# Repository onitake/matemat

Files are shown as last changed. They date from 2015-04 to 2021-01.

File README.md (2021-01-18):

# Matemat

The Matemat is a vending machine for carbonated soft drinks.

It is based on an old vending machine with all its electronics replaced by new
custom-build circuit boards.

All hardware and software was designed by members of
[CCC Basel](http://www.ccc-basel.ch) and released in the form of circuit
diagrams, printed circuit board layouts and source code for anyone to use and
modify. Refer to the LICENSE file for details.

The name "Matemat" is a portmanteau of "mate" (as in mate tea) and "automat"
(the German word for vending machine). The device is mainly intended to dispense
mate tea based soft drinks, but may be used for other types of beverages too.

## Structure

The heart of the vending machine is a Raspberry Pi model 3 or zero or later,
with a custom CAN interface board on its GPIO header.

See [CAN Hat](https://github.com/onitake/canhat) for more information.

## Firmware

Some of the modules require firmware. There is a makefile in each module's
firmware directory to build and flash the firmware to the integrated
microcontroller

Before building, you need to check out the CAN driver source code, which is
referenced as a Git submodule.

Run the following commands in the checked out repository:

```shell
git submodule init
git submodule update
```

## Modules

The Matemat components are highly modular. Individual circuits are connected by
CAN bus, and can be extended as needed.

### drive

Single-motor driver.

Attached directly to each bottle release mechanism. Requires only power supply
wires for the motor and the CAN bus line.

### power

Motor driver board and power supply.

Alternative to the drive board. Uses the existing machine wiring instead of
power + CAN.

### control

Old central control board. Obsolete.

### feedback

End switch feedback interface.

Senses the status of the end switches and sends CAN bus messages on changes.

This module requires firmware. Connect an Atmel programmer to the ISP header,
change into the firmware directory `feedback/firmware/` and run:

```shell
make flash
```

### poweriface

Interface between CAN bus and power board.

This module requires firmware. Connect an Atmel programmer to the ISP header,
change into the firmware directory `poweriface/firmware/` and run:

```shell
make flash
```

### sensor

Environment sensor interface.

### wiring

Wring schema of the old vending machine.

## Bus

### Topology

All modules are connected via a CAN bus. It is highly recommended to wire them
by means of shielded twisted-pair cable with a nominal impedance of 120Ω.
At the very least, you need a cable with three wires to ensure a good ground
connection between all modules.

To allow for easy wiring, six-pole screw terminals are mounted to the PCBs.
Two poles are intended for the positive CAN bus line, two for the negative line
and two for the shield. They are internally connected together.

### Wiring

To achieve a continuous bus topology, connect only two cables to each module.
Make sure CAN H is connected to CAN H and CAN L to CAN L. Crossover is not
supported on the CAN bus. When wiring is complete, you should end up with a
continuous bus that is tapped at each module. Attach 120Ω resistors (preferably
1% or better) to the ends of the bus.

The final wiring should look like this:

```
┌───────────┐   ┌───────────┐   ┌───────────┐
│  module1  │   │  module2  │   │  module3  │
│           │   │           │   │           │
│H L ⏚ H L ⏚│   │H L ⏚ H L ⏚│   │H L ⏚ H L ⏚│
└╥─╥─╥─╥─╥─╥┘   └╥─╥─╥─╥─╥─╥┘   └╥─╥─╥─╥─╥─╥┘
 ╰━╯   └╥┘╱      └╥┘╱  └╥┘╱      └╥┘╱  ╰━╯
 120Ω   ║╱        ║╱    ║╱        ║╱   120Ω
        ╚═════════╝     ╚═════════╝
```

### Protocol

Bus communication only makes use of basic CAN features. No higher-level
protocols such as CiA, EtherCAN, VSCP or similar are required.

Normal 11-bit CAN adressing mode is used. For messages that support RTR, any
module can send a remote transmission request and the addressed module will
respond with the described message. A module may also send the message
without being probed.

This is the list of supported message IDs:

| Message ID | Sender | Receiver | RTR Support? |Data Length | Data Format | Description |
|---|---|---|---|---|---|---|
| 0x10 | feedback | any | yes | 2 | 0b00000KJI 0bHGFEDCBA | Feedback module status report (A..E = end switch D..H, F..J = empty switch D..H, K = reset switch, 0 = off, 1 = on) |
| 0x11 | poweriface | any | yes | 2 | 0bHHHHHHHH 0bLLLLLLLL | Power module status report (0xHHLL are the contents of the 16-bit shift register) |
| 0x21 | controller | poweriface | no | 1 | 0b00000MMM | Start dispensing from slot M (1-5) or stop all dispensers (M = 0) |
| 0x4f | any | any | no | 1 | 0b0000000E | Enable (E = 1) or disable (E = 0) automatic status updates on all modules |

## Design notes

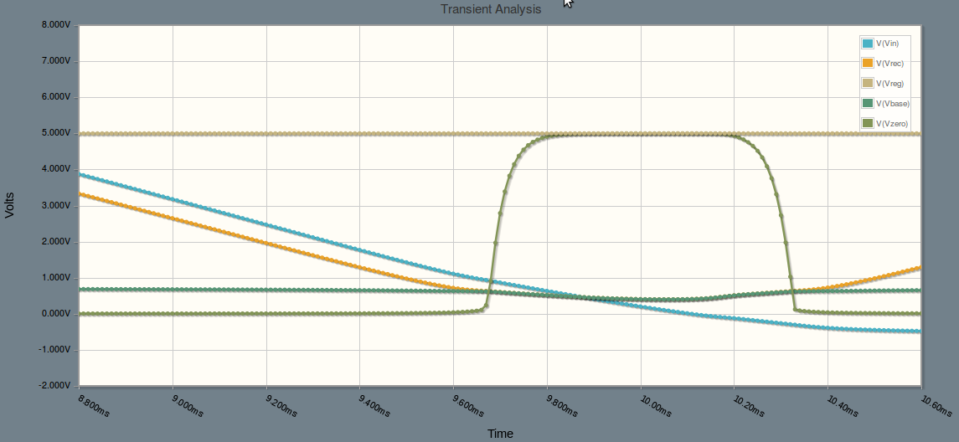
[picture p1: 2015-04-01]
zerocross.png

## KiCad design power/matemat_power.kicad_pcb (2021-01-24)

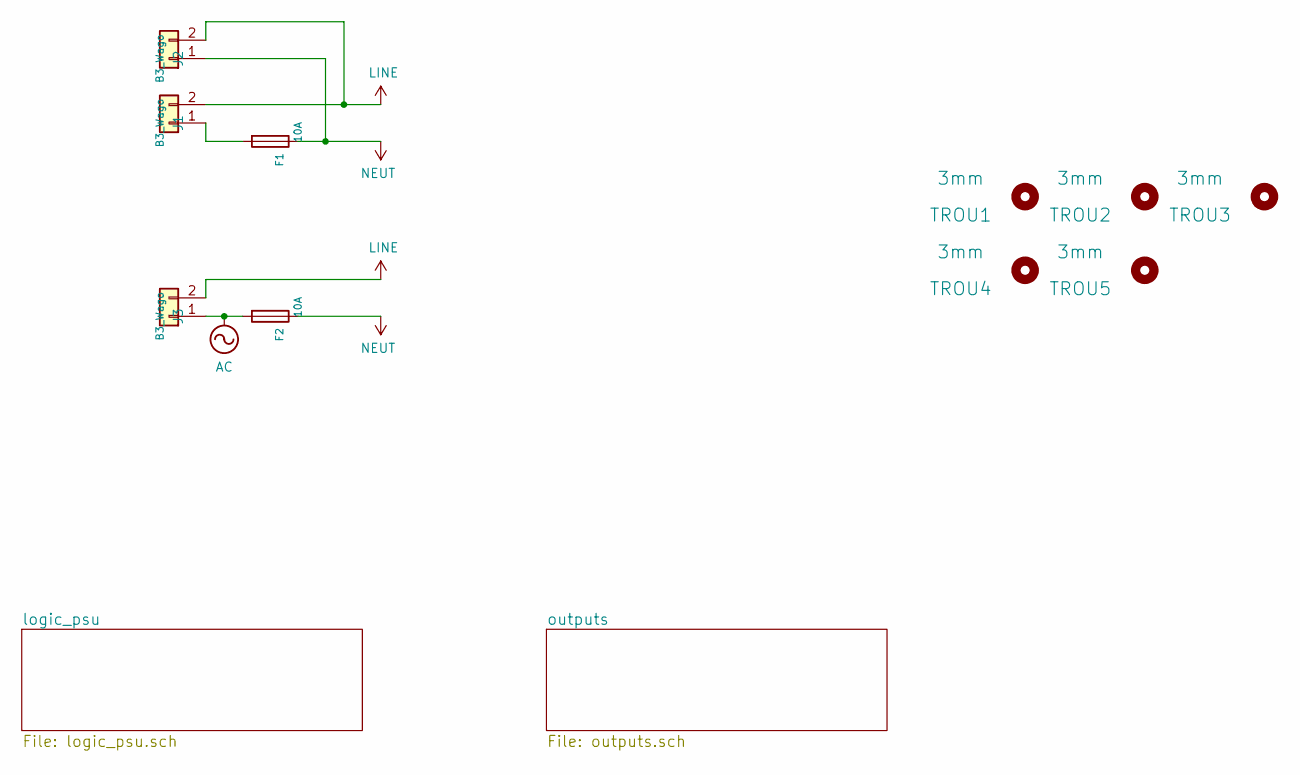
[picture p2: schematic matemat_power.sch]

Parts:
F1, F2: 10A; Fuseholder_Cylinder-5x20mm_Schurter_0031_8201_Horizontal_Op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
J1, J2, J3: B3_Wago; TerminalBlock_WAGO_236-402_1x02_P5.00mm_45Degree
TROU1, TROU2, TROU3, TROU4, TROU5: 3mm; MountingHole_3.2mm_M3

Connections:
AC: F2.2, J3.1; also elsewhere on the board
LINE: J1.2, J2.2, J3.2; also elsewhere on the board
NEUT: F1.1, F2.1, J2.1; also elsewhere on the board
unnamed: F1.2, J1.1

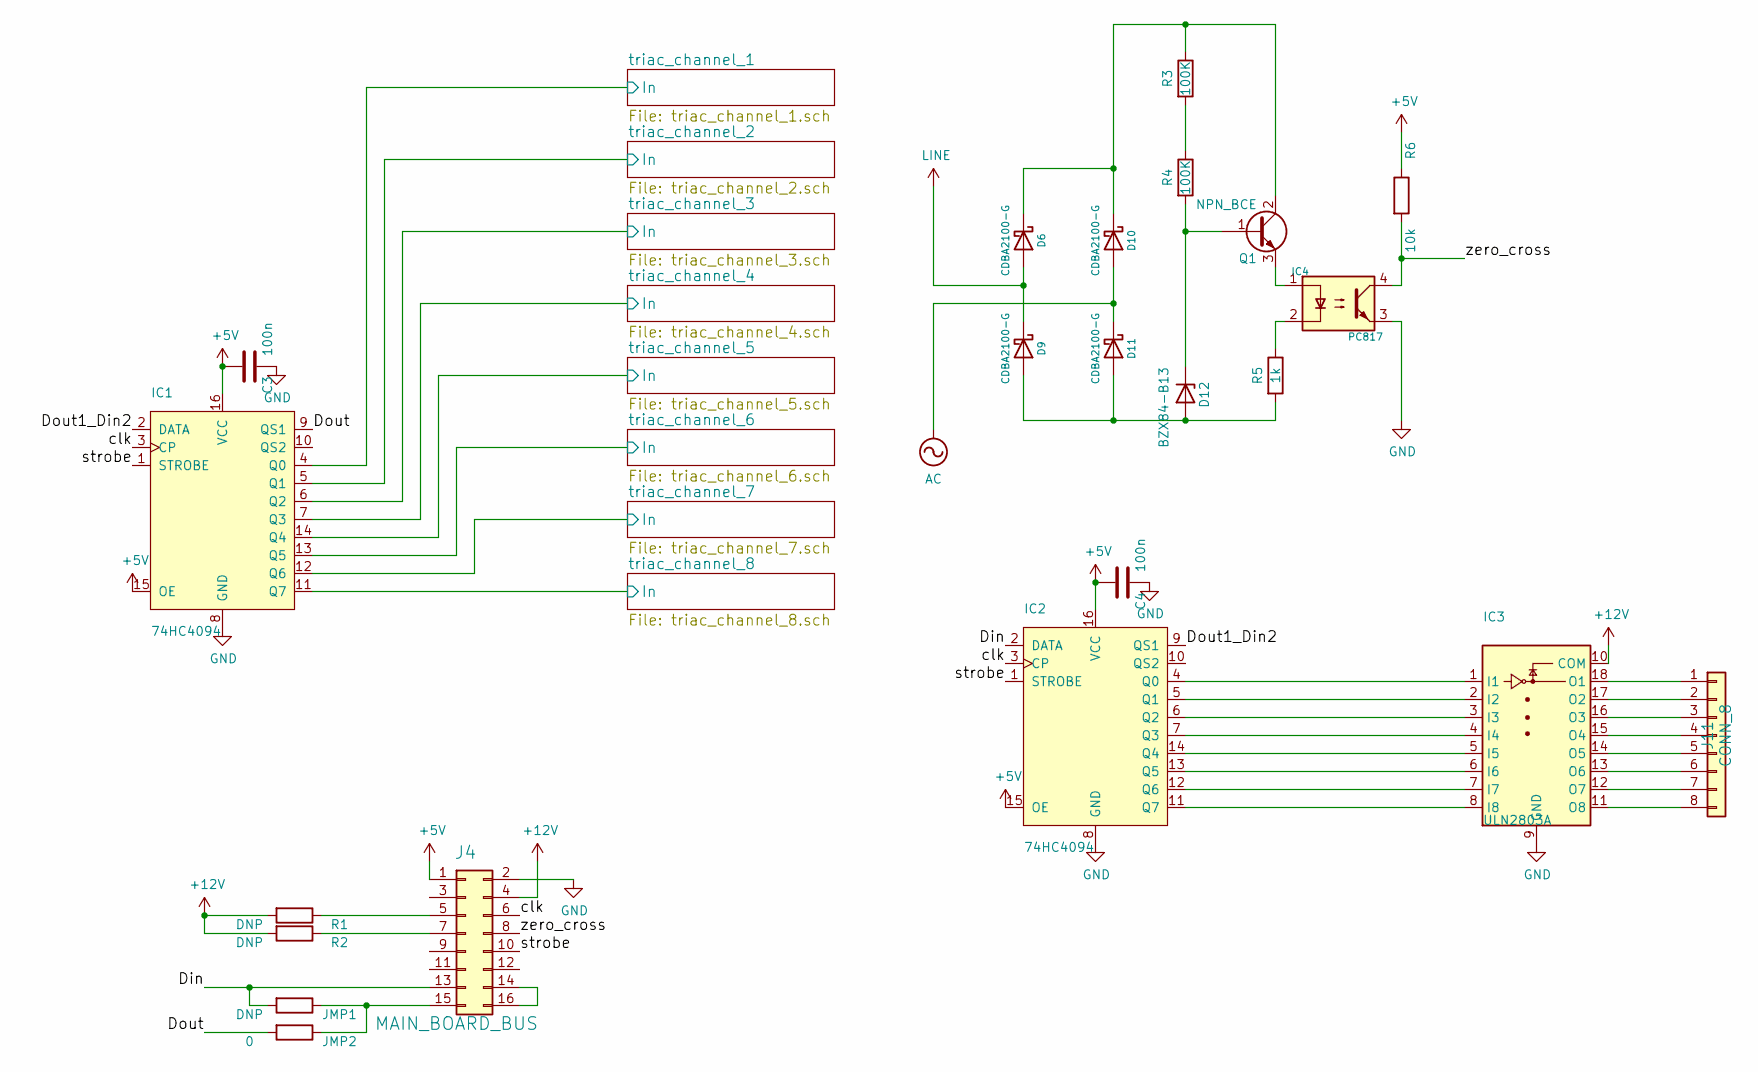
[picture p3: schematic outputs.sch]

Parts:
C3, C4: 100n; C_0805_2012Metric_Pad1.18x1.45mm_HandSolder
D6, D9, D10, D11: CDBA2100-G; D_SMA
D12: BZX84-B13; D_SOT-23_ANK
IC1, IC2: 74HC4094; SOIC-16_3.9x9.9mm_P1.27mm
IC3: ULN2803A; SOIC-18W_7.5x11.6mm_P1.27mm
IC4: PC817; DIP-4_W7.62mm
J4: MAIN_BOARD_BUS; PinHeader_2x08_P2.54mm_Vertical
J11: CONN_8; TerminalBlock_Phoenix_MPT-0,5-8-2.54_1x08_P2.54mm_Horizontal
JMP1: DNP; R_0603_1608Metric_Pad0.98x0.95mm_HandSolder
JMP2: 0; R_0603_1608Metric_Pad0.98x0.95mm_HandSolder
Q1: NPN_BCE; TO-220-3_Vertical
R1, R2: DNP; R_0603_1608Metric_Pad0.98x0.95mm_HandSolder
R3, R4: 100K; R_Axial_DIN0309_L9.0mm_D3.2mm_P12.70mm_Horizontal
R5: 1k; R_0805_2012Metric_Pad1.20x1.40mm_HandSolder
R6: 10k; R_0805_2012Metric_Pad1.20x1.40mm_HandSolder

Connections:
+5V: C3.2, C4.2, IC1.15 (OE), IC1.16 (VCC), IC2.15 (OE), IC2.16 (VCC), J4.1, R6.1
+12V: IC3.10 (COM), J4.4, R1.2, R2.2; also elsewhere on the board
/outputs/Din: IC2.2 (DATA), J4.13, JMP1.2
/outputs/Dout: IC1.9 (QS1), JMP2.2
/outputs/Dout1_Din2: IC1.2 (DATA), IC2.9 (QS1)
/outputs/clk: IC1.3 (CP), IC2.3 (CP), J4.6
/outputs/strobe: IC1.1 (STROBE), IC2.1 (STROBE), J4.10
/outputs/triac_channel_1/In: IC1.4 (Q0); also elsewhere on the board
/outputs/triac_channel_2/In: IC1.5 (Q1); also elsewhere on the board
/outputs/triac_channel_3/In: IC1.6 (Q2); also elsewhere on the board
/outputs/triac_channel_4/In: IC1.7 (Q3); also elsewhere on the board
/outputs/triac_channel_5/In: IC1.14 (Q4); also elsewhere on the board
/outputs/triac_channel_6/In: IC1.13 (Q5); also elsewhere on the board
/outputs/triac_channel_7/In: IC1.12 (Q6); also elsewhere on the board
/outputs/triac_channel_8/In: IC1.11 (Q7); also elsewhere on the board
/outputs/zero_cross: IC4.4, J4.8, R6.2
AC: D10.2 (A), D11.1 (K); also elsewhere on the board
GND: C3.1, C4.1, IC1.8 (GND), IC2.8 (GND), IC3.9 (GND), IC4.3, J4.2; also elsewhere on the board
LINE: D6.2 (A), D9.1 (K); also elsewhere on the board
unnamed: D6.1 (K), D10.1 (K), Q1.2 (C), R3.1
unnamed: D9.2 (A), D11.2 (A), D12.2 (A), R5.2
unnamed: D12.1 (K), Q1.1 (B), R4.2
unnamed: IC2.4 (Q0), IC3.1 (I1)
unnamed: IC2.5 (Q1), IC3.2 (I2)
unnamed: IC2.6 (Q2), IC3.3 (I3)
unnamed: IC2.7 (Q3), IC3.4 (I4)
unnamed: IC2.11 (Q7), IC3.8 (I8)
unnamed: IC2.12 (Q6), IC3.7 (I7)
unnamed: IC2.13 (Q5), IC3.6 (I6)
unnamed: IC2.14 (Q4), IC3.5 (I5)
unnamed: IC3.11 (O8), J11.8
unnamed: IC3.12 (O7), J11.7
unnamed: IC3.13 (O6), J11.6
unnamed: IC3.14 (O5), J11.5
unnamed: IC3.15 (O4), J11.4
unnamed: IC3.16 (O3), J11.3
unnamed: IC3.17 (O2), J11.2
unnamed: IC3.18 (O1), J11.1
unnamed: IC4.1, Q1.3 (E)
unnamed: IC4.2, R5.1
unnamed: J4.5, R1.1
unnamed: J4.7, R2.1
unnamed: J4.14, J4.16
unnamed: J4.15, JMP1.1, JMP2.1
unnamed: R3.2, R4.1

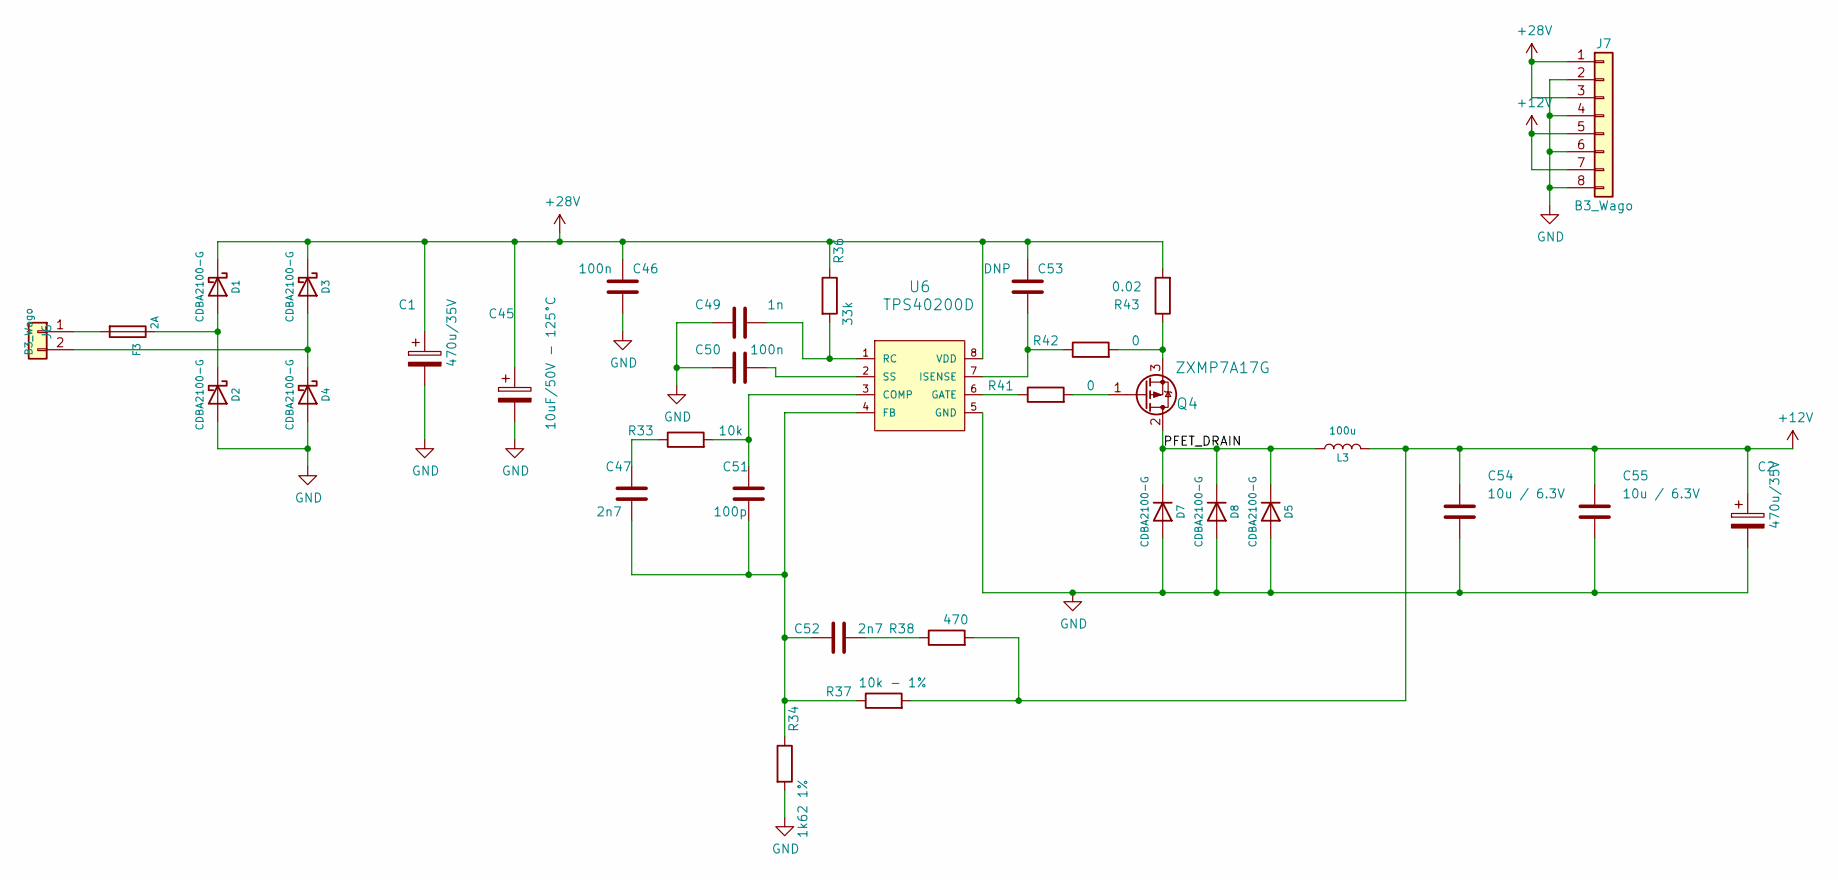
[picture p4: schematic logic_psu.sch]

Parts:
C1, C2: 470u/35V; CP_Radial_D10.0mm_P5.00mm
C45: 10uF/50V - 125°C; CP_Radial_D10.0mm_P5.00mm
C46, C50: 100n; C_0805_2012Metric_Pad1.18x1.45mm_HandSolder
C47, C52: 2n7; C_0805_2012Metric_Pad1.18x1.45mm_HandSolder
C49: 1n; C_0805_2012Metric_Pad1.18x1.45mm_HandSolder
C51: 100p; C_0805_2012Metric_Pad1.18x1.45mm_HandSolder
C53: DNP; C_0805_2012Metric_Pad1.18x1.45mm_HandSolder
C54, C55: 10u / 6.3V; C_0805_2012Metric_Pad1.18x1.45mm_HandSolder
D1, D2, D3, D4, D5, D7, D8: CDBA2100-G; D_SMA
F3: 2A; Fuseholder_Cylinder-5x20mm_Schurter_0031_8201_Horizontal_Op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
J6: B3_Wago; TerminalBlock_WAGO_236-402_1x02_P5.00mm_45Degree
J7: B3_Wago; TerminalBlock_WAGO_236-408_1x08_P5.00mm_45Degree
L3: 100u; L_Toroid_Vertical_L22.4mm_W10.2mm_P7.90mm_Vishay_TJ4
Q4: ZXMP7A17G; SOT-223-3_TabPin2
R33: 10k; R_0805_2012Metric_Pad1.20x1.40mm_HandSolder
R34: 1k62 1%; R_0805_2012Metric_Pad1.20x1.40mm_HandSolder
R36: 33k; R_0805_2012Metric_Pad1.20x1.40mm_HandSolder
R37: 10k - 1%; R_0805_2012Metric_Pad1.20x1.40mm_HandSolder
R38: 470; R_0805_2012Metric_Pad1.20x1.40mm_HandSolder
R41, R42: 0; R_0805_2012Metric_Pad1.20x1.40mm_HandSolder
R43: 0.02; R_2010_5025Metric_Pad1.40x2.65mm_HandSolder
U6: TPS40200D; SOIC-8_3.9x4.9mm_P1.27mm

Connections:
+12V: C2.1, C54.1, C55.1, J7.5, J7.7, L3.2, R37.2, R38.2; also elsewhere on the board
+28V: C1.1, C45.1, C46.1, C53.1, D1.1 (K), D3.1 (K), J7.1, J7.3, R36.1, R43.2, U6.8 (VDD)
/logic_psu/PFET_DRAIN: D5.1 (K), D7.1 (K), D8.1 (K), L3.1, Q4.2 (D)
GND: C1.2, C2.2, C45.2, C46.2, C49.1, C50.1, C54.2, C55.2, D2.2 (A), D4.2 (A), D5.2 (A), D7.2 (A), D8.2 (A), J7.2, J7.4, J7.6, J7.8, R34.2, U6.5 (GND); also elsewhere on the board
unnamed: C47.1, R33.1
unnamed: C47.2, C51.2, C52.1, R34.1, R37.1, U6.4 (FB)
unnamed: C49.2, R36.2, U6.1 (RC)
unnamed: C50.2, U6.2 (SS)
unnamed: C51.1, R33.2, U6.3 (COMP)
unnamed: C52.2, R38.1
unnamed: C53.2, R42.1, U6.7 (ISENSE)
unnamed: D1.2 (A), D2.1 (K), F3.1
unnamed: D3.2 (A), D4.1 (K), J6.2
unnamed: F3.2, J6.1
unnamed: Q4.1 (G), R41.2
unnamed: Q4.3 (S), R42.2, R43.1
unnamed: R41.1, U6.6 (GATE)

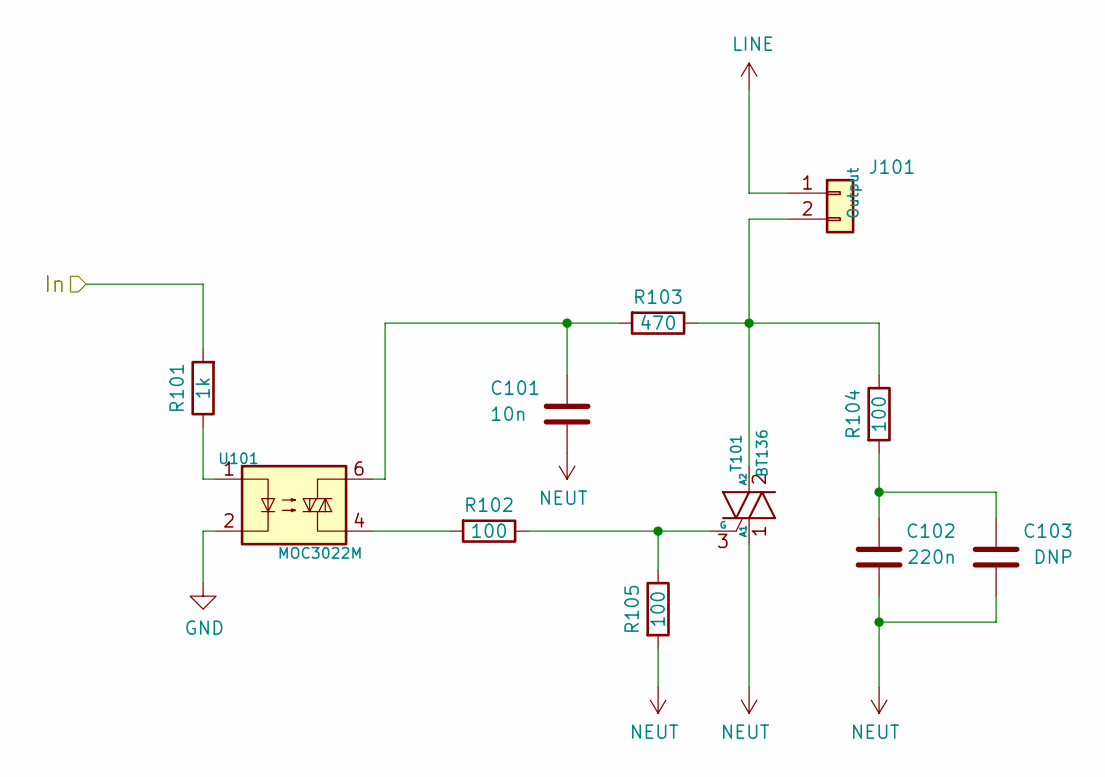
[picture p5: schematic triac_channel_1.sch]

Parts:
C101: 10n; C_Rect_L7.0mm_W2.5mm_P5.00mm
C102: 220n; C_Rect_L18.0mm_W5.0mm_P15.00mm_FKS3_FKP3
C103: DNP; C_Rect_L13.0mm_W4.0mm_P10.00mm_FKS3_FKP3_MKS4
J101: Output; TerminalBlock_WAGO_236-402_1x02_P5.00mm_45Degree
R101: 1k; R_0805_2012Metric_Pad1.20x1.40mm_HandSolder
R102, R104: 100; R_Axial_DIN0309_L9.0mm_D3.2mm_P12.70mm_Horizontal
R103: 470; R_Axial_DIN0309_L9.0mm_D3.2mm_P12.70mm_Horizontal
R105: 100; R_0805_2012Metric_Pad1.20x1.40mm_HandSolder
T101: BT136; TO-220-3_Vertical
U101: MOC3022M; DIP-6_W7.62mm_LongPads

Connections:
/outputs/triac_channel_1/In: R101.2; also elsewhere on the board
GND: U101.2; also elsewhere on the board
LINE: J101.1; also elsewhere on the board
NEUT: C101.2, C102.2, C103.2, R105.2, T101.1 (A1); also elsewhere on the board
unnamed: C101.1, R103.2, U101.6
unnamed: C102.1, C103.1, R104.2
unnamed: J101.2, R103.1, R104.1, T101.2 (A2)
unnamed: R101.1, U101.1
unnamed: R102.1, R105.1, T101.3 (G)
unnamed: R102.2, U101.4

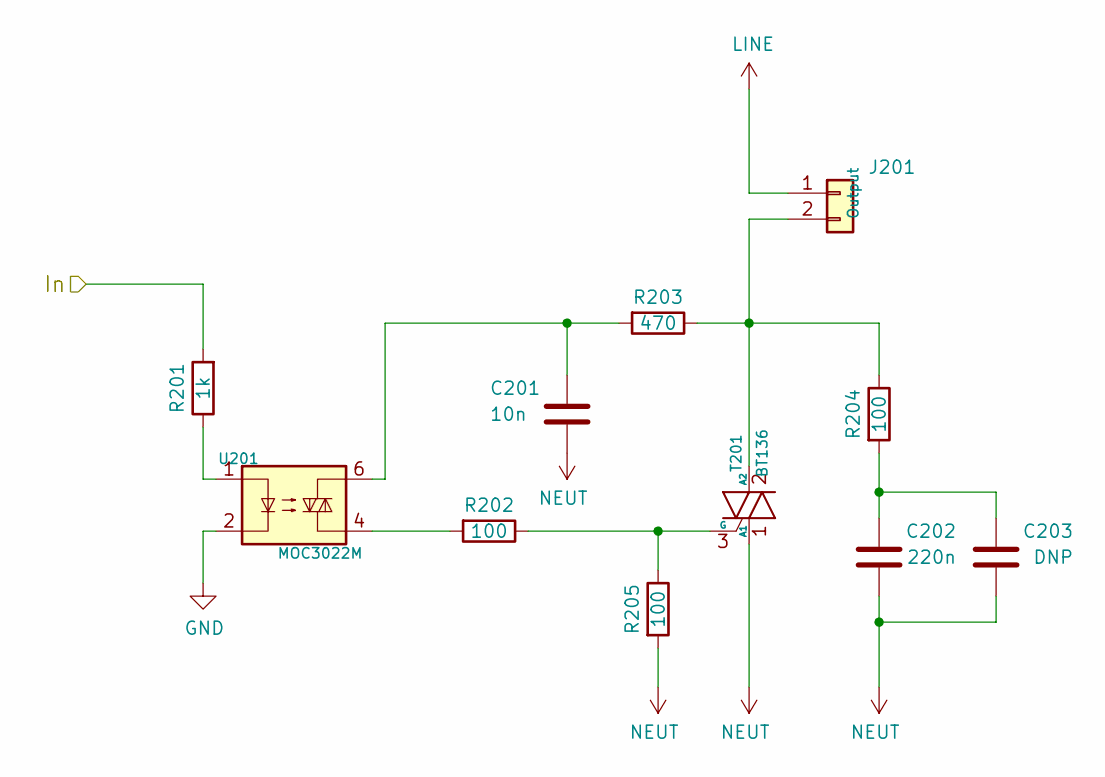
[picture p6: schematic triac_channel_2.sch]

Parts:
C201: 10n; C_Rect_L7.0mm_W2.5mm_P5.00mm
C202: 220n; C_Rect_L18.0mm_W5.0mm_P15.00mm_FKS3_FKP3
C203: DNP; C_Rect_L13.0mm_W4.0mm_P10.00mm_FKS3_FKP3_MKS4
J201: Output; TerminalBlock_WAGO_236-402_1x02_P5.00mm_45Degree
R201: 1k; R_0805_2012Metric_Pad1.20x1.40mm_HandSolder
R202, R204: 100; R_Axial_DIN0309_L9.0mm_D3.2mm_P12.70mm_Horizontal
R203: 470; R_Axial_DIN0309_L9.0mm_D3.2mm_P12.70mm_Horizontal
R205: 100; R_0805_2012Metric_Pad1.20x1.40mm_HandSolder
T201: BT136; TO-220-3_Vertical
U201: MOC3022M; DIP-6_W7.62mm_LongPads

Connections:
/outputs/triac_channel_2/In: R201.2; also elsewhere on the board
GND: U201.2; also elsewhere on the board
LINE: J201.1; also elsewhere on the board
NEUT: C201.2, C202.2, C203.2, R205.2, T201.1 (A1); also elsewhere on the board
unnamed: C201.1, R203.2, U201.6
unnamed: C202.1, C203.1, R204.2
unnamed: J201.2, R203.1, R204.1, T201.2 (A2)
unnamed: R201.1, U201.1
unnamed: R202.1, R205.1, T201.3 (G)
unnamed: R202.2, U201.4

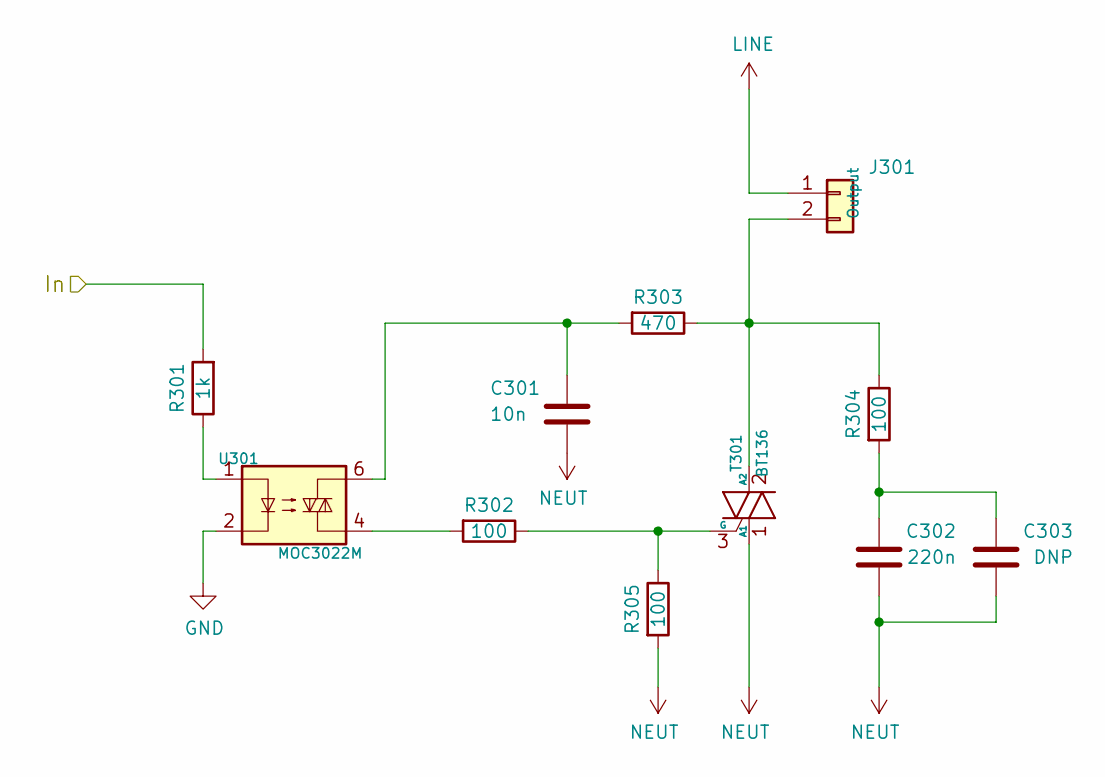
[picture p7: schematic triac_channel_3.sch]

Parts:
C301: 10n; C_Rect_L7.0mm_W2.5mm_P5.00mm
C302: 220n; C_Rect_L18.0mm_W5.0mm_P15.00mm_FKS3_FKP3
C303: DNP; C_Rect_L13.0mm_W4.0mm_P10.00mm_FKS3_FKP3_MKS4
J301: Output; TerminalBlock_WAGO_236-402_1x02_P5.00mm_45Degree
R301: 1k; R_0805_2012Metric_Pad1.20x1.40mm_HandSolder
R302, R304: 100; R_Axial_DIN0309_L9.0mm_D3.2mm_P12.70mm_Horizontal
R303: 470; R_Axial_DIN0309_L9.0mm_D3.2mm_P12.70mm_Horizontal
R305: 100; R_0805_2012Metric_Pad1.20x1.40mm_HandSolder
T301: BT136; TO-220-3_Vertical
U301: MOC3022M; DIP-6_W7.62mm_LongPads

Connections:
/outputs/triac_channel_3/In: R301.2; also elsewhere on the board
GND: U301.2; also elsewhere on the board
LINE: J301.1; also elsewhere on the board
NEUT: C301.2, C302.2, C303.2, R305.2, T301.1 (A1); also elsewhere on the board
unnamed: C301.1, R303.2, U301.6
unnamed: C302.1, C303.1, R304.2
unnamed: J301.2, R303.1, R304.1, T301.2 (A2)
unnamed: R301.1, U301.1
unnamed: R302.1, R305.1, T301.3 (G)
unnamed: R302.2, U301.4

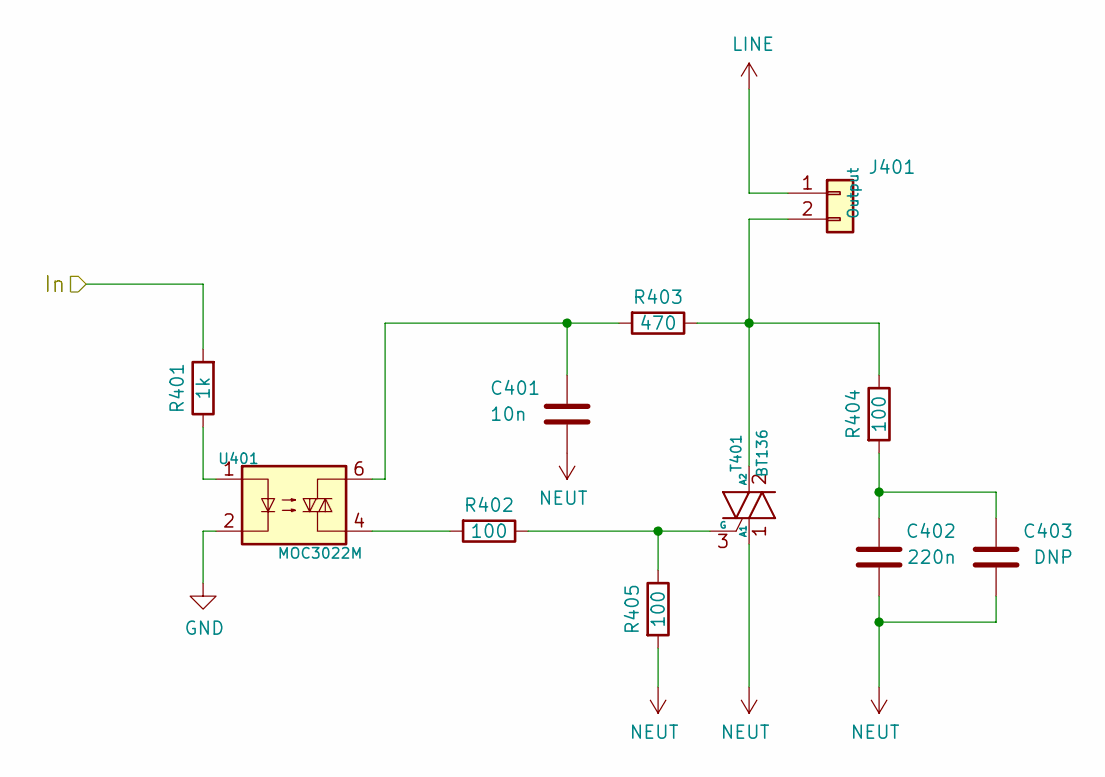
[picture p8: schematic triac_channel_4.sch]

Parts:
C401: 10n; C_Rect_L7.0mm_W2.5mm_P5.00mm
C402: 220n; C_Rect_L18.0mm_W5.0mm_P15.00mm_FKS3_FKP3
C403: DNP; C_Rect_L13.0mm_W4.0mm_P10.00mm_FKS3_FKP3_MKS4
J401: Output; TerminalBlock_WAGO_236-402_1x02_P5.00mm_45Degree
R401: 1k; R_0805_2012Metric_Pad1.20x1.40mm_HandSolder
R402, R404: 100; R_Axial_DIN0309_L9.0mm_D3.2mm_P12.70mm_Horizontal
R403: 470; R_Axial_DIN0309_L9.0mm_D3.2mm_P12.70mm_Horizontal
R405: 100; R_0805_2012Metric_Pad1.20x1.40mm_HandSolder
T401: BT136; TO-220-3_Vertical
U401: MOC3022M; DIP-6_W7.62mm_LongPads

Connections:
/outputs/triac_channel_4/In: R401.2; also elsewhere on the board
GND: U401.2; also elsewhere on the board
LINE: J401.1; also elsewhere on the board
NEUT: C401.2, C402.2, C403.2, R405.2, T401.1 (A1); also elsewhere on the board
unnamed: C401.1, R403.2, U401.6
unnamed: C402.1, C403.1, R404.2
unnamed: J401.2, R403.1, R404.1, T401.2 (A2)
unnamed: R401.1, U401.1
unnamed: R402.1, R405.1, T401.3 (G)
unnamed: R402.2, U401.4

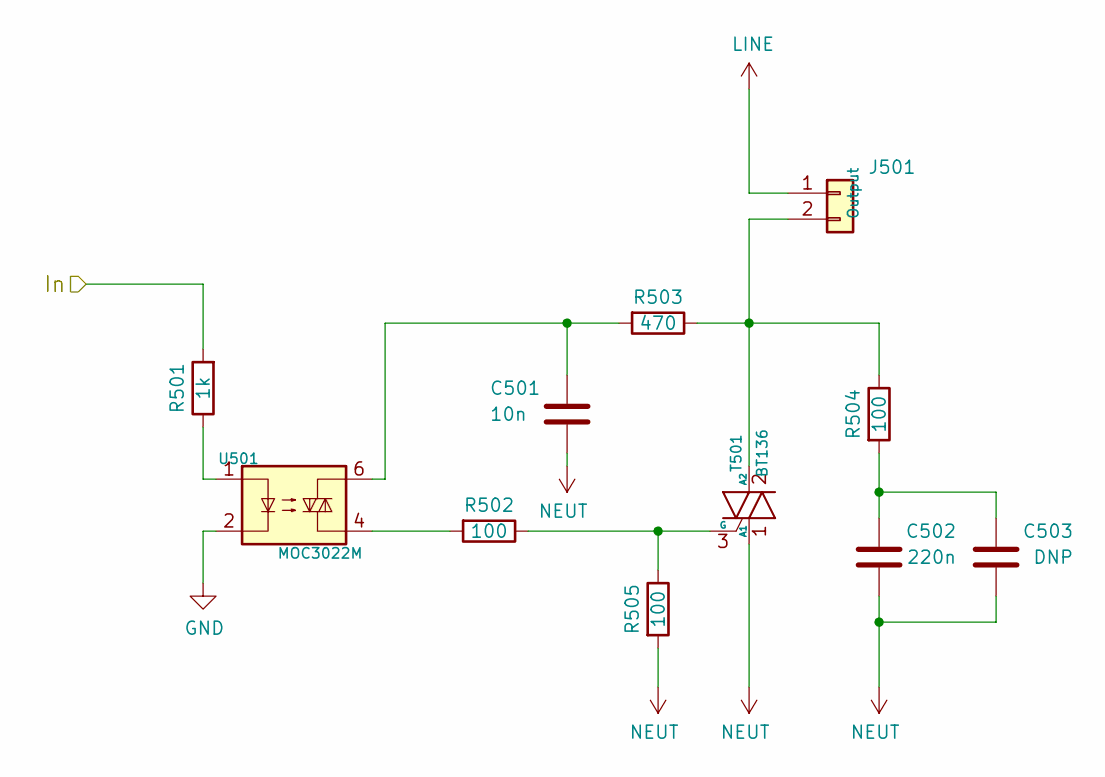
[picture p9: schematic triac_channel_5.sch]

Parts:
C501: 10n; C_Rect_L7.0mm_W2.5mm_P5.00mm
C502: 220n; C_Rect_L18.0mm_W5.0mm_P15.00mm_FKS3_FKP3
C503: DNP; C_Rect_L13.0mm_W4.0mm_P10.00mm_FKS3_FKP3_MKS4
J501: Output; TerminalBlock_WAGO_236-402_1x02_P5.00mm_45Degree
R501: 1k; R_0805_2012Metric_Pad1.20x1.40mm_HandSolder
R502, R504: 100; R_Axial_DIN0309_L9.0mm_D3.2mm_P12.70mm_Horizontal
R503: 470; R_Axial_DIN0309_L9.0mm_D3.2mm_P12.70mm_Horizontal
R505: 100; R_0805_2012Metric_Pad1.20x1.40mm_HandSolder
T501: BT136; TO-220-3_Vertical
U501: MOC3022M; DIP-6_W7.62mm_LongPads

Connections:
/outputs/triac_channel_5/In: R501.2; also elsewhere on the board
GND: U501.2; also elsewhere on the board
LINE: J501.1; also elsewhere on the board
NEUT: C501.2, C502.2, C503.2, R505.2, T501.1 (A1); also elsewhere on the board
unnamed: C501.1, R503.2, U501.6
unnamed: C502.1, C503.1, R504.2
unnamed: J501.2, R503.1, R504.1, T501.2 (A2)
unnamed: R501.1, U501.1
unnamed: R502.1, R505.1, T501.3 (G)
unnamed: R502.2, U501.4

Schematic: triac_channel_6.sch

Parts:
C601: 10n; C_Rect_L7.0mm_W2.5mm_P5.00mm
C602: 220n; C_Rect_L18.0mm_W5.0mm_P15.00mm_FKS3_FKP3
C603: DNP; C_Rect_L13.0mm_W4.0mm_P10.00mm_FKS3_FKP3_MKS4
J601: Output; TerminalBlock_WAGO_236-402_1x02_P5.00mm_45Degree
R601: 1k; R_0805_2012Metric_Pad1.20x1.40mm_HandSolder
R602, R604: 100; R_Axial_DIN0309_L9.0mm_D3.2mm_P12.70mm_Horizontal
R603: 470; R_Axial_DIN0309_L9.0mm_D3.2mm_P12.70mm_Horizontal
R605: 100; R_0805_2012Metric_Pad1.20x1.40mm_HandSolder
T601: BT136; TO-220-3_Vertical
U601: MOC3022M; DIP-6_W7.62mm_LongPads

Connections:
/outputs/triac_channel_6/In: R601.2; also elsewhere on the board
GND: U601.2; also elsewhere on the board
LINE: J601.1; also elsewhere on the board
NEUT: C601.2, C602.2, C603.2, R605.2, T601.1 (A1); also elsewhere on the board
unnamed: C601.1, R603.2, U601.6
unnamed: C602.1, C603.1, R604.2
unnamed: J601.2, R603.1, R604.1, T601.2 (A2)
unnamed: R601.1, U601.1
unnamed: R602.1, R605.1, T601.3 (G)
unnamed: R602.2, U601.4

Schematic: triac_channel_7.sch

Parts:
C701: 10n; C_Rect_L7.0mm_W2.5mm_P5.00mm
C702: 220n; C_Rect_L18.0mm_W5.0mm_P15.00mm_FKS3_FKP3
C703: DNP; C_Rect_L13.0mm_W4.0mm_P10.00mm_FKS3_FKP3_MKS4
J701: Output; TerminalBlock_WAGO_236-402_1x02_P5.00mm_45Degree
R701: 1k; R_0805_2012Metric_Pad1.20x1.40mm_HandSolder
R702, R704: 100; R_Axial_DIN0309_L9.0mm_D3.2mm_P12.70mm_Horizontal
R703: 470; R_Axial_DIN0309_L9.0mm_D3.2mm_P12.70mm_Horizontal
R705: 100; R_0805_2012Metric_Pad1.20x1.40mm_HandSolder
T701: BT136; TO-220-3_Vertical
U701: MOC3022M; DIP-6_W7.62mm_LongPads

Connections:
/outputs/triac_channel_7/In: R701.2; also elsewhere on the board
GND: U701.2; also elsewhere on the board
LINE: J701.1; also elsewhere on the board
NEUT: C701.2, C702.2, C703.2, R705.2, T701.1 (A1); also elsewhere on the board
unnamed: C701.1, R703.2, U701.6
unnamed: C702.1, C703.1, R704.2
unnamed: J701.2, R703.1, R704.1, T701.2 (A2)
unnamed: R701.1, U701.1
unnamed: R702.1, R705.1, T701.3 (G)
unnamed: R702.2, U701.4

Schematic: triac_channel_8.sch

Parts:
C801: 10n; C_Rect_L7.0mm_W2.5mm_P5.00mm
C802: 220n; C_Rect_L18.0mm_W5.0mm_P15.00mm_FKS3_FKP3
C803: DNP; C_Rect_L13.0mm_W4.0mm_P10.00mm_FKS3_FKP3_MKS4
J801: Output; TerminalBlock_WAGO_236-402_1x02_P5.00mm_45Degree
R801: 1k; R_0805_2012Metric_Pad1.20x1.40mm_HandSolder
R802, R804: 100; R_Axial_DIN0309_L9.0mm_D3.2mm_P12.70mm_Horizontal
R803: 470; R_Axial_DIN0309_L9.0mm_D3.2mm_P12.70mm_Horizontal
R805: 100; R_0805_2012Metric_Pad1.20x1.40mm_HandSolder
T801: BT136; TO-220-3_Vertical
U801: MOC3022M; DIP-6_W7.62mm_LongPads

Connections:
/outputs/triac_channel_8/In: R801.2; also elsewhere on the board
GND: U801.2; also elsewhere on the board
LINE: J801.1; also elsewhere on the board
NEUT: C801.2, C802.2, C803.2, R805.2, T801.1 (A1); also elsewhere on the board
unnamed: C801.1, R803.2, U801.6
unnamed: C802.1, C803.1, R804.2
unnamed: J801.2, R803.1, R804.1, T801.2 (A2)
unnamed: R801.1, U801.1
unnamed: R802.1, R805.1, T801.3 (G)
unnamed: R802.2, U801.4

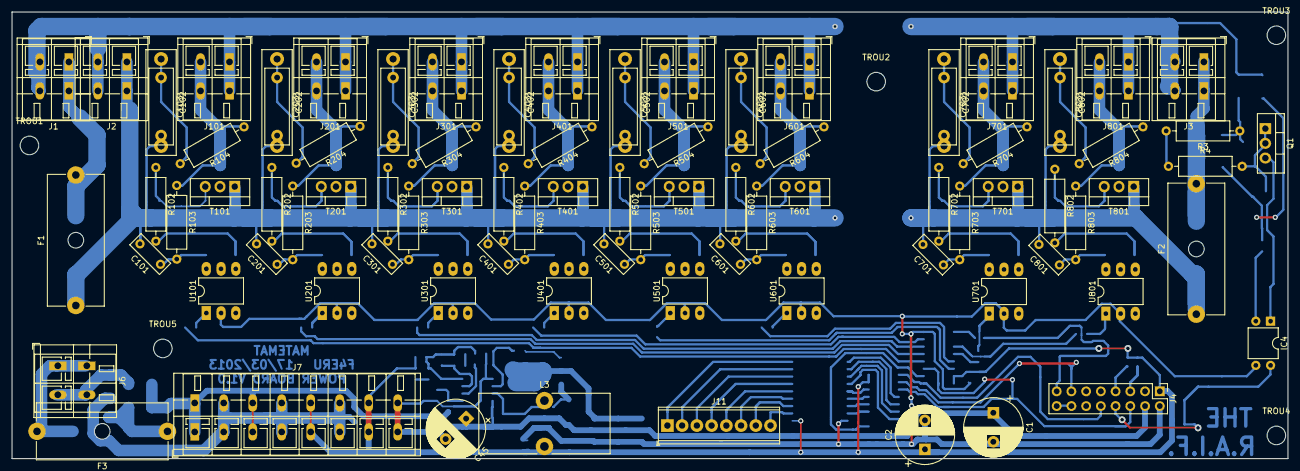
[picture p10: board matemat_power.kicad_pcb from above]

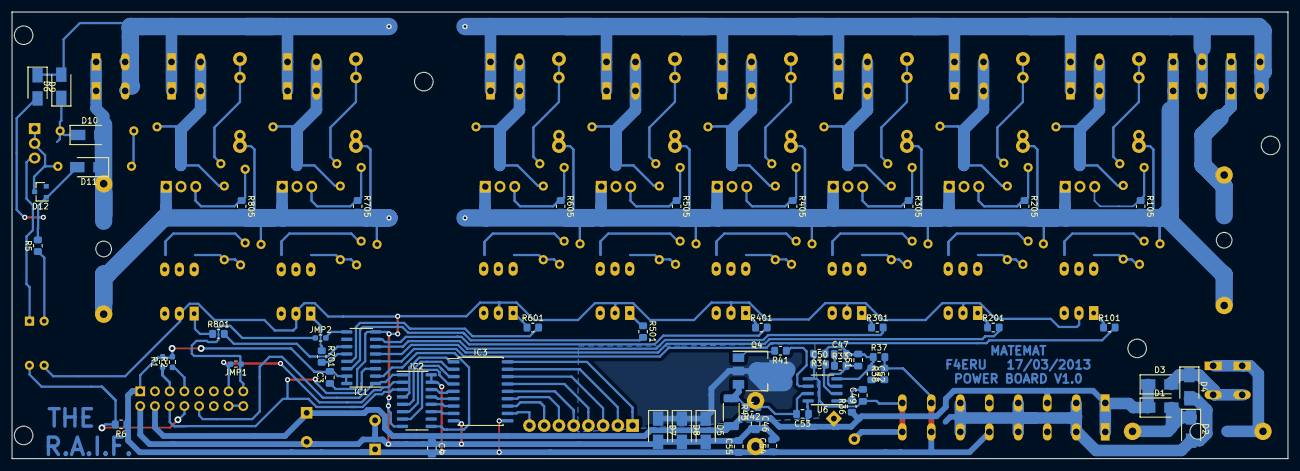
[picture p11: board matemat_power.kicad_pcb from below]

Board: 2 copper layers, 220.0 x 77.0 mm, 153 parts (58 on the bottom side), 110 nets.

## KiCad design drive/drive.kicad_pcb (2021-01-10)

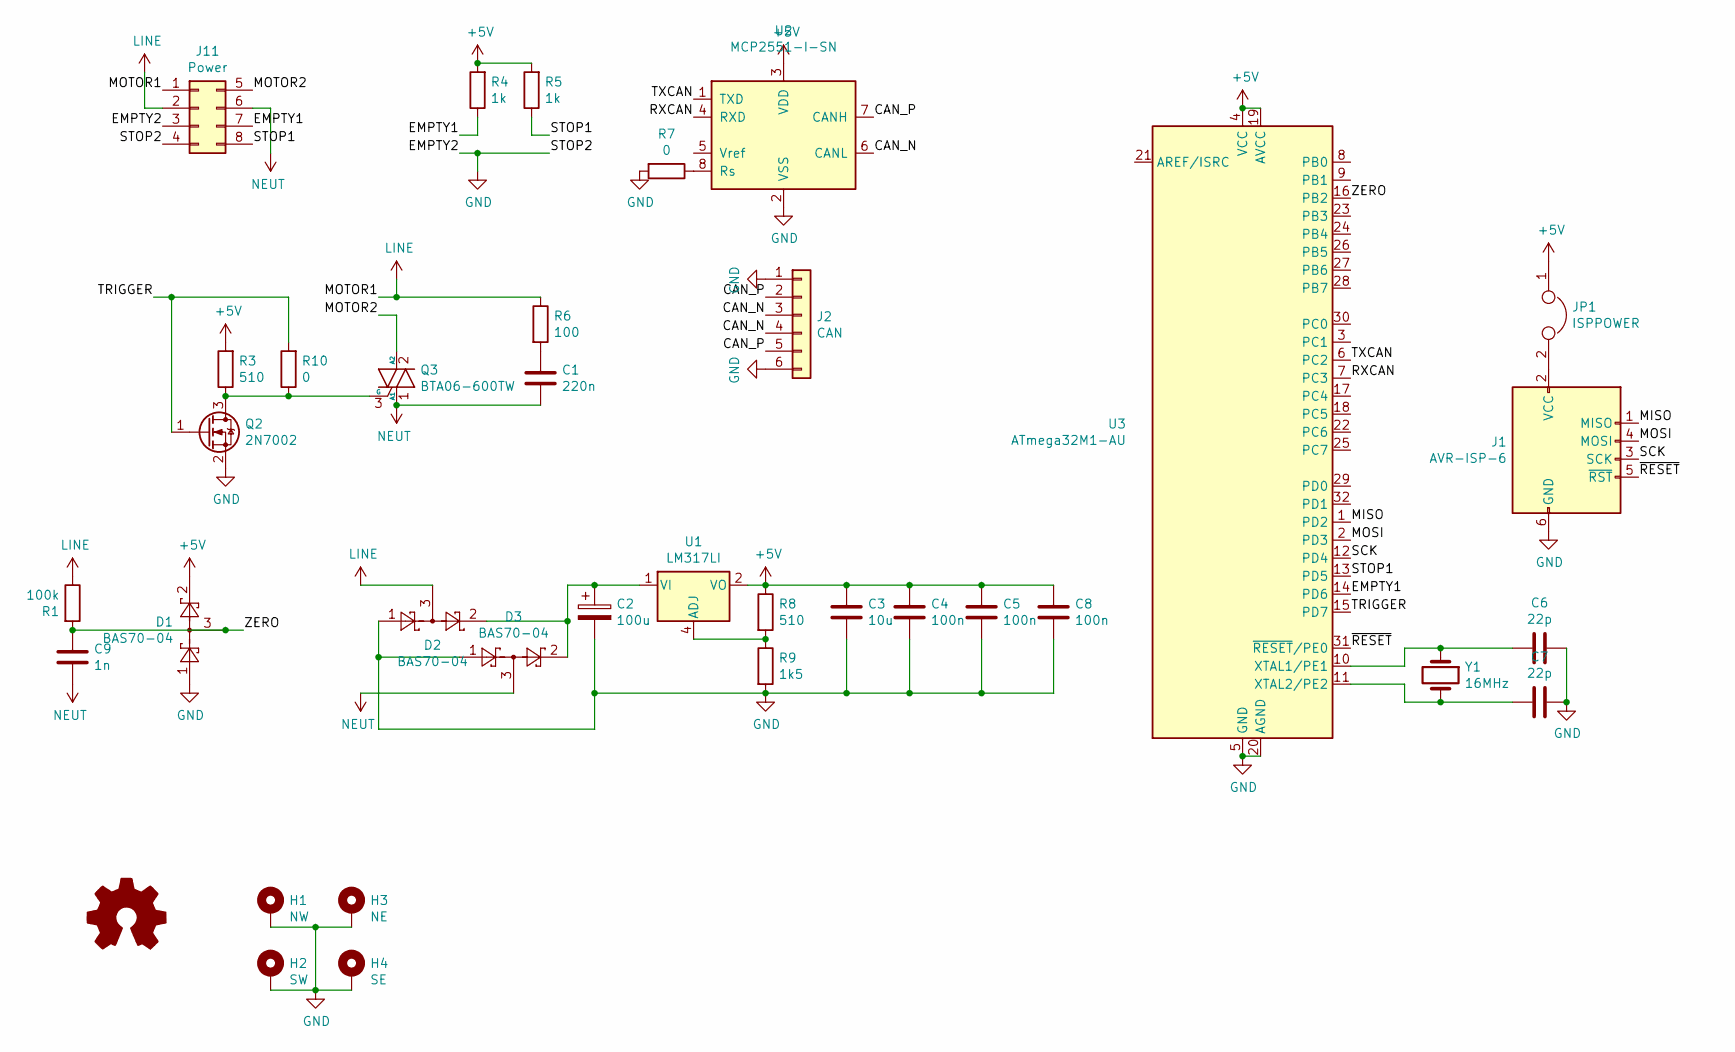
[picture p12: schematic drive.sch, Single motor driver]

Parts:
C1: 220n; C_Rect_L7.2mm_W2.5mm_P5.00mm_FKS2_FKP2_MKS2_MKP2
C2: 100u; CP_Radial_D8.0mm_P3.50mm
C3: 10u; C_0805_2012Metric_Pad1.15x1.40mm_HandSolder
C4, C5, C8: 100n; C_0805_2012Metric_Pad1.15x1.40mm_HandSolder
C6, C7: 22p; C_0805_2012Metric_Pad1.15x1.40mm_HandSolder
C9: 1n; C_0805_2012Metric_Pad1.15x1.40mm_HandSolder
D1, D2, D3: BAS70-04; SOT-23
H1: NW; MountingHole_3.2mm_M3_ISO7380_Pad
H2: SW; MountingHole_3.2mm_M3_ISO7380_Pad
H3: NE; MountingHole_3.2mm_M3_ISO7380_Pad
H4: SE; MountingHole_3.2mm_M3_ISO7380_Pad
J1: AVR-ISP-6; PinHeader_2x03_P2.54mm_Vertical
J2: CAN; TerminalBlock_TE_282834-6_1x06_P2.54mm_Horizontal
J11: Power; Molex_Mini-Fit_Jr_5569-08A2_2x04_P4.20mm_Horizontal
JP1: ISPPOWER; PinHeader_1x02_P2.54mm_Vertical
Q2: 2N7002; SOT-23
Q3: BTA06-600TW; TO-220-3_Vertical
R1: 100k; R_0805_2012Metric_Pad1.15x1.40mm_HandSolder
R3, R8: 510; R_0805_2012Metric_Pad1.15x1.40mm_HandSolder
R4, R5: 1k; R_0805_2012Metric_Pad1.15x1.40mm_HandSolder
R6: 100; R_Axial_DIN0207_L6.3mm_D2.5mm_P7.62mm_Horizontal
R7, R10: 0; R_0805_2012Metric_Pad1.15x1.40mm_HandSolder
R9: 1k5; R_0805_2012Metric_Pad1.15x1.40mm_HandSolder
U1: LM317LI; SOIC-8_3.9x4.9mm_P1.27mm
U2: MCP2551-I-SN; SOIC-8_3.9x4.9mm_P1.27mm
U3: ATmega32M1-AU; TQFP-32_7x7mm_P0.8mm
Y1: 16MHz; Crystal_SMD_HC49-SD

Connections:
+5V: C3.1, C4.1, C5.1, C8.1, D1.2, JP1.1, R3.2, R4.2, R5.2, R8.1, U1.2 (VO), U1.3 (VO), U1.6 (VO), U1.7 (VO), U2.3 (VDD), U3.4 (VCC), U3.19 (AVCC)
/CAN_N: J2.3, J2.4, U2.6 (CANL)
/CAN_P: J2.2, J2.5, U2.7 (CANH)
/EMPTY1: J11.7, R4.1, U3.14 (PD6)
/MISO: J1.1 (MISO), U3.1 (PD2)
/MOSI: J1.4 (MOSI), U3.2 (PD3)
/MOTOR2: J11.5, Q3.2 (A2)
/RXCAN: U2.4 (RXD), U3.7 (PC3)
/SCK: J1.3 (SCK), U3.12 (PD4)
/STOP1: J11.8, R5.1, U3.13 (PD5)
/TRIGGER: Q2.1 (G), R10.2, U3.15 (PD7)
/TXCAN: U2.1 (TXD), U3.6 (PC2)
/ZERO: C9.1, D1.3, R1.2, U3.16 (PB2)
/~RESET: J1.5 (~RST), U3.31 (~RESET~/PE0)
GND: C2.2, C3.2, C4.2, C5.2, C6.1, C7.1, C8.2, D1.1, D2.1, D3.1, H1.1, H2.1, H3.1, H4.1, J1.6 (GND), J2.1, J2.6, J11.3, J11.4, Q2.2 (S), R7.2, R9.2, U2.2 (VSS), U3.5 (GND), U3.20 (AGND)
LINE: D2.3, J11.1, J11.2, R1.1, R6.1
NEUT: C1.2, C9.2, D3.3, J11.6, Q3.1 (A1)
unnamed: C1.1, R6.2
unnamed: C2.1, D2.2, D3.2, U1.1 (VI)
unnamed: C6.2, U3.10 (XTAL1/PE1), Y1.1
unnamed: C7.2, U3.11 (XTAL2/PE2), Y1.2
unnamed: J1.2 (VCC), JP1.2
unnamed: Q2.3 (D), Q3.3 (G), R3.1, R10.1
unnamed: R7.1, U2.8 (Rs)
unnamed: R8.2, R9.1, U1.4 (ADJ)

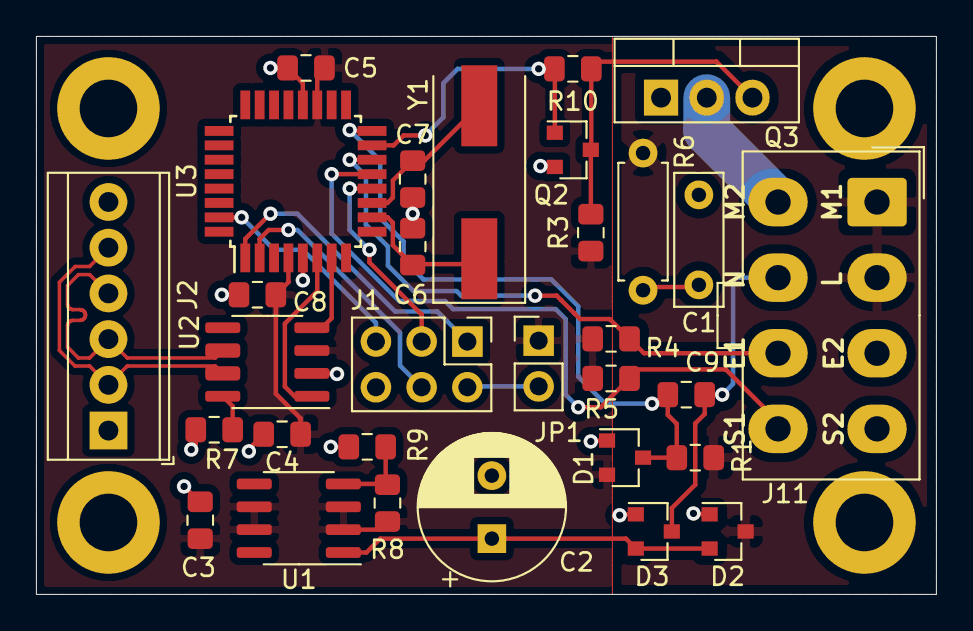
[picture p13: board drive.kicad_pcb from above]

Board: 2 copper layers, 50.0 x 31.0 mm, 35 parts (0 on the bottom side), 25 nets.

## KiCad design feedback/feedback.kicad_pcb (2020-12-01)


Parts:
C1, C3, C6, C7: 100n; C_0805_2012Metric_Pad1.15x1.40mm_HandSolder
C2: 1u; C_0805_2012Metric_Pad1.15x1.40mm_HandSolder
C4, C5: 22p; C_0805_2012Metric_Pad1.15x1.40mm_HandSolder
H1: NW; MountingHole_3.2mm_M3_ISO7380
H2: SW; MountingHole_3.2mm_M3_ISO7380
H3: NE; MountingHole_3.2mm_M3_ISO7380
H4: SE; MountingHole_3.2mm_M3_ISO7380
J1: 12V; TerminalBlock_TE_282834-2_1x02_P2.54mm_Horizontal
J2: C; Molex_MLX-42002_10-84-4150_3x5-Pin_P6.35mm_Vertical
J3: AVR-ISP-6; PinHeader_2x03_P2.54mm_Vertical
J4: Conn_01x08; TerminalBlock_TE_282834-8_1x08_P2.54mm_Horizontal
J5: USW; TerminalBlock_TE_1-282834-2_1x12_P2.54mm_Horizontal
JP1: Jumper; PinHeader_1x02_P2.54mm_Vertical
OHW1: Logo_Open_Hardware_Small; OSHW-Logo2_7.3x6mm_SilkScreen
R1: 1k2/1%; R_0805_2012Metric_Pad1.15x1.40mm_HandSolder
R2: 3k3/1%; R_0805_2012Metric_Pad1.15x1.40mm_HandSolder
R3: 0; R_0805_2012Metric_Pad1.15x1.40mm_HandSolder
RN1, RN2, RN3: 1k; R_Array_Convex_4x1206
U1: ATmega32M1-AU; TQFP-32_7x7mm_P0.8mm
U2: LM317_SOT-223; SOT-223-3_TabPin2
U3: MCP2551-I-SN; SOIC-8_3.9x4.9mm_P1.27mm
Y1: 16MHz; Crystal_SMD_HC49-SD

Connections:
+5V: C2.1, C3.1, C6.1, C7.1, JP1.1, R1.1, RN1.5 (R4.2), RN1.6 (R3.2), RN1.7 (R2.2), RN1.8 (R1.2), RN2.5 (R4.2), RN2.6 (R3.2), RN2.7 (R2.2), RN2.8 (R1.2), RN3.5 (R4.2), RN3.6 (R3.2), RN3.7 (R2.2), RN3.8 (R1.2), U1.4 (VCC), U1.19 (AVCC), U2.2 (VO), U3.3 (VDD)
+12V: C1.1, J1.1, J4.8, U2.3 (VI)
/CAN_N: J4.3, J4.4, U3.6 (CANL)
/CAN_P: J4.2, J4.5, U3.7 (CANH)
/D_EMPTY: J2.15, J5.12, RN2.4 (R4.1), U1.26 (PB5)
/D_END: J2.1, J5.1, RN1.1 (R1.1), U1.8 (PB0)
/E_EMPTY: J2.12, J5.9, RN3.1 (R1.1), U1.27 (PB6)
/E_END: J2.4, J5.3, RN1.2 (R2.1), U1.9 (PB1)
/F_EMPTY: J2.9, J5.7, RN3.2 (R2.1), U1.28 (PB7)
/F_END: J2.13, J5.10, RN1.3 (R3.1), U1.16 (PB2)
/G_EMPTY: J2.6, J5.4, RN3.3 (R3.1), U1.30 (PC0)
/G_END: J2.10, J5.8, RN2.2 (R2.1), U1.23 (PB3)
/H_EMPTY: J2.2, J2.3, J5.2, RN2.1 (R1.1), U1.22 (PC6)
/H_END: J2.7, J5.5, RN2.3 (R3.1), U1.24 (PB4)
/MISO: J3.1 (MISO), U1.1 (PD2)
/MOSI: J3.4 (MOSI), U1.2 (PD3)
/RESET: J3.5 (~RST), U1.31 (~RESET~/PE0)
/RXCAN: U1.7 (PC3), U3.4 (RXD)
/SCK: J3.3 (SCK), U1.12 (PD4)
/SW_RESET: J2.14, J5.11, RN1.4 (R4.1), U1.17 (PC4)
/TXCAN: U1.6 (PC2), U3.1 (TXD)
GND: C1.2, C2.2, C3.2, C4.1, C5.1, C6.2, C7.2, J1.2, J2.5, J2.8, J3.6 (GND), J4.1, J4.6, J4.7, J5.6, R2.2, R3.2, U1.5 (GND), U1.20 (AGND), U3.2 (VSS)
unnamed: C4.2, U1.10 (XTAL1/PE1), Y1.1
unnamed: C5.2, U1.11 (XTAL2/PE2), Y1.2
unnamed: J3.2 (VCC), JP1.2
unnamed: R1.2, R2.1, U2.1 (ADJ)
unnamed: R3.1, U3.8 (Rs)


Board: 2 copper layers, 74.0 x 35.0 mm, 27 parts (0 on the bottom side), 27 nets.

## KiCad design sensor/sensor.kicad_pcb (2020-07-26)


Board: 2 copper layers, 46.5 x 34.0 mm, 47 parts (0 on the bottom side), 39 nets.

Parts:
C1, C2: 22p; C_0805_2012Metric_Pad1.15x1.40mm_HandSolder
C3: 10u; C_0805_2012Metric_Pad1.15x1.40mm_HandSolder
C4, C9, C10, C18: 100n; C_0805_2012Metric_Pad1.15x1.40mm_HandSolder
C5, C6, C7, C8, C11, C12, C13, C14, C16, C17: 10n; C_0805_2012Metric_Pad1.15x1.40mm_HandSolder
C15: 100n/0R; C_0805_2012Metric_Pad1.15x1.40mm_HandSolder
D1: POWER; LED_0805_2012Metric_Pad1.15x1.40mm_HandSolder
H1: NW; MountingHole_3.2mm_M3_Pad
H2: NE; MountingHole_3.2mm_M3_Pad
H3: SW; MountingHole_3.2mm_M3_Pad
J1: 12V; TerminalBlock_TE_282834-2_1x02_P2.54mm_Horizontal
J2: CAN; TerminalBlock_TE_282834-6_1x06_P2.54mm_Horizontal
J4: AVR-ISP-6; PinHeader_2x03_P2.54mm_Vertical
J5: SENSOR IN; PinHeader_1x10_P2.54mm_Vertical
J6: SENSOR VCC; PinHeader_1x10_P2.54mm_Vertical
J7: SENSOR GND; PinHeader_1x10_P2.54mm_Vertical
JP1: ISP POWER; PinHeader_1x02_P2.54mm_Vertical
L1: 10u; L_0805_2012Metric_Pad1.15x1.40mm_HandSolder
R1, R2, R3, R4, R5, R6, R7, R8, R9, R10, R11: 0; R_0805_2012Metric_Pad1.15x1.40mm_HandSolder
R12: 470; R_0805_2012Metric_Pad1.15x1.40mm_HandSolder
R13: DNP/0; R_0805_2012Metric_Pad1.15x1.40mm_HandSolder
U1: ATmega32M1-AU; TQFP-32_7x7mm_P0.8mm
U2: MCP2551-I-SN; SOIC-8_3.9x4.9mm_P1.27mm
U3: LM2937xMP; SOT-223-3_TabPin2
Y1: 16MHz; Crystal_SMD_HC49-SD

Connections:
/ADC5: C8.1, R5.2, U1.16
/ADC8: C7.1, R4.2, U1.17
/ADC9: C6.1, R3.2, U1.18
/ADC10: C5.1, R2.2, U1.22
/AIN0: J5.7, R2.1
/AIN1: J5.8, R3.1
/AIN2: J5.9, R4.1
/AIN3: J5.10, R5.1
/AREF: C15.1, U1.21
/CAN_HISPEED: R1.2, U1.14
/CAN_N: J2.2, J2.5, U2.6
/CAN_P: J2.3, J2.4, U2.7
/CAN_RXD: U1.7, U2.4
/CAN_TXD: U1.6, U2.1
/DIN0: J5.1, R6.1
/DIN1: J5.2, R7.1
/DIN2: J5.3, R8.1
/DIN3: J5.4, R9.1
/DIN4: J5.5, R10.1
/DIN5: J5.6, R11.1
/ISP_MISO: J4.1, U1.1
/ISP_MOSI: J4.4, U1.2
/ISP_SCK: J4.3, U1.12
/PCINT5: C16.1, R10.2, U1.26
/PCINT6: C14.1, R9.2, U1.27
/PCINT8: C12.1, R7.2, U1.30
/PCINT15: C17.1, R11.2, U1.25
/PCINT16: C13.1, R8.2, U1.29
/PCINT17: C11.1, R6.2, U1.32
/~ISP_RESET: J4.5, U1.31
GND: C1.2, C2.1, C3.2, C4.2, C5.2, C6.2, C7.2, C8.2, C9.2, C10.2, C11.2, C12.2, C13.2, C14.2, C15.2, C16.2, C17.2, C18.2, D1.1, H1.1, H2.1, H3.1, J1.1, J2.1, J2.6, J4.6, J7.1, J7.2, J7.3, J7.4, J7.5, J7.6, J7.7, J7.8, J7.9, J7.10, U1.5, U1.20, U2.2, U3.2
unnamed: C1.1, U1.10, Y1.1
unnamed: C2.2, U1.11, Y1.2
unnamed: C18.1, J1.2, R13.2, U3.1
unnamed: D1.2, R12.1
unnamed: J4.2, JP1.2
unnamed: R1.1, U2.8
VAA: C10.1, L1.2, U1.19
VCC: C3.1, C4.1, C9.1, J6.1, J6.2, J6.3, J6.4, J6.5, J6.6, J6.7, J6.8, J6.9, J6.10, JP1.1, L1.1, R12.2, R13.1, U1.4, U2.3, U3.3

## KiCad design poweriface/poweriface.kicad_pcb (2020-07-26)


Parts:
C1, C2: 22p; C_0805_2012Metric_Pad1.15x1.40mm_HandSolder
C3: 10u; C_0805_2012Metric_Pad1.15x1.40mm_HandSolder
C4, C5, C6: 100n; C_0805_2012Metric_Pad1.15x1.40mm_HandSolder
J1: Power Board; PinSocket_2x08_P2.54mm_Vertical
J2: CAN; TerminalBlock_TE_282834-4_1x04_P2.54mm_Horizontal
J3: CAN_SHIELD; TerminalBlock_TE_282834-6_1x06_P2.54mm_Horizontal
J4: AVR-ISP-6; PinHeader_2x03_P2.54mm_Vertical
JP1: ISP Power; PinHeader_1x02_P2.54mm_Vertical
R1, R2, R3, R4: 1k; R_0805_2012Metric_Pad1.15x1.40mm_HandSolder
R5, R6: 0; R_0805_2012Metric_Pad1.15x1.40mm_HandSolder
R7: DNP; R_0805_2012Metric_Pad1.15x1.40mm_HandSolder
U1: ATmega32M1-AU; TQFP-32_7x7mm_P0.8mm
U2: MCP2551-I-SN; SOIC-8_3.9x4.9mm_P1.27mm
Y1: 16MHz; Crystal_SMD_HC49-SD

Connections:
+5V: C3.1, C4.1, C5.1, C6.1, J1.1 (5V), JP1.1, U1.4 (VCC), U1.19 (AVCC), U2.3 (VDD)
/CAN_N: J2.1, J2.4, J3.2, J3.5, U2.6 (CANL)
/CAN_P: J2.2, J2.3, J3.3, J3.4, U2.7 (CANH)
/CLK: J1.6 (CAN+), R1.2
/DIN: J1.13 (RX/MOSI), R3.2
/DOUT: J1.15 (TX/MISO), R4.2
/HISPEED: R7.1, U1.14 (PD6)
/MISOISP: J4.1 (MISO), U1.1 (PD2)
/MOSIISP: J4.4 (MOSI), U1.2 (PD3)
/RXCAN: U1.7 (PC3), U2.4 (RXD)
/SCKISP: J4.3 (SCK), R5.2, U1.12 (PD4)
/STROBE: J1.10, R2.2
/TXCAN: U1.6 (PC2), U2.1 (TXD)
/ZCROSS: J1.8 (CAN-), R5.1, U1.13 (PD5)
/~RESET: J4.5 (~RST), U1.31 (~RESET~/PE0)
GND: C1.1, C2.1, C3.2, C4.2, C5.2, C6.2, J1.2 (GND), J3.1, J3.6, J4.6 (GND), R6.1, U1.5 (GND), U1.20 (AGND), U2.2 (VSS)
unnamed: C1.2, U1.10 (XTAL1/PE1), Y1.1
unnamed: C2.2, U1.11 (XTAL2/PE2), Y1.2
unnamed: J4.2 (VCC), JP1.2
unnamed: R1.1, U1.16 (PB2)
unnamed: R2.1, U1.23 (PB3)
unnamed: R3.1, U1.24 (PB4)
unnamed: R4.1, U1.26 (PB5)
unnamed: R6.2, R7.2, U2.8 (Rs)


Board: 2 copper layers, 25.0 x 42.5 mm, 20 parts (1 on the bottom side), 24 nets.

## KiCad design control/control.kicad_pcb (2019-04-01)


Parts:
C1, C2, C3, C4, C7, C8, C9, C10, C11, C12, C13, C14, C15, C16, C17, C18, C19, C20, C21, C22, C23, C25, C27, C28, C29, C30, C31, C33: 100n; C_0805_HandSoldering
C5, C6: 22p; C_0805_HandSoldering
C24: 4.7u; C_Radial_D5_L11_P2.5
C26: 22u; C_Radial_D5_L11_P2.5
C32: 10u; C_Radial_D5_L11_P2.5
D1, D2, D3, D4, D5: LED805; LED-0805
IC1: TJA1040; SOIC-8_3.9x4.9mm_Pitch1.27mm
IC2: DNP MAX481CSA; SOIC-8_3.9x4.9mm_Pitch1.27mm
IC3, IC5: ST232BD; SOIC-16_3.9x9.9mm_Pitch1.27mm
IC4: ATMEGA128-A; TQFP-64_14x14mm_Pitch0.8mm
IC6: FT232RL; SSOP-28_5.3x10.2mm_Pitch0.65mm
J4: POWER; Pin_Header_Straight_2x08
JP1: 1-2 FLASH EN; Pin_Header_Straight_1x03
JP2: RESET; Pin_Header_Straight_1x02
L1: 100u; wuerth_elektronik_v5-WE-PD2_S
P1: SENSOR; Pin_Header_Straight_2x08
P2: I2C0; Pin_Header_Straight_2x05
P3: I2C1; Pin_Header_Straight_2x05
P4: I2C2; Pin_Header_Straight_2x05
P5: COIN; Pin_Header_Straight_1x17
P6: CONN_02X13; Pin_Header_Straight_2x13
P7: ISP; Pin_Header_Straight_2x03
P8: 12V; Bornier_B2_Phoenix
P9: 5V; Bornier_B2_Phoenix
P10, P13: DB9; DB9MCS
P11: USB_B
P12: USB_OTG; USB_Micro-B
R1, R6, R7, R8, R9, R10, R11, R20, R31, R34, R37, R40, R48, R52, R54, R56, R58, R67, R68, R71: DNP; R_0805_HandSoldering
R2, R3, R4, R5, R30: 0; R_0805_HandSoldering
R12, R13, R14, R15, R16, R17, R18, R19, R22, R23, R24, R25, R26, R27, R32, R33, R35, R38, R41, R49, R50, R64, R65, R66, R69, R70: 1k; R_0805_HandSoldering
R21, R51, R53, R55, R60, R61, R63: 10k; R_0805_HandSoldering
R28, R29, R42, R43, R44, R45, R46, R47: 100; R_0805_HandSoldering
R36, R39: 1k8; R_0805_HandSoldering
R62: 4.7k; R_0805_HandSoldering
TP1, TP2, TP3, TP4: 3mm; MountingHole_3mm
U1: DNP LM2940-N 5V; SOT-223
X1: 16MHz; Q_49U3HMS

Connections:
+12V: C31.1, C32.1, J4.4 (VBatt), P2.9, P2.10, P3.9, P3.10, P4.9, P4.10, P5.11, P6.1, P6.3, P8.2, R10.1, U1.1 (VI)
/ANALOG_0: C18.1, IC4.61 (PF0(ADC0)), R13.2, R56.1
/ANALOG_1: C16.1, IC4.60 (PF1(ADC1)), R15.2, R52.1
/ANALOG_2: C14.1, IC4.59 (PF2(ADC2)), R17.2, R40.1
/ANALOG_3: C12.1, IC4.58 (PF3(ADC3)), R19.2, R34.1
/BILL_IN_ACK: IC4.36 ((A9)PC1), P6.18, R53.1
/BILL_IN_INH: IC4.37 ((A10)PC2), P6.16, R51.1
/BILL_IN_REJ: IC4.35 ((A8)PC0), P6.20, R55.1
/BILL_OUT_ABN: IC4.38 ((A11)PC3), P6.13, R41.1
/BILL_OUT_BUSY: IC4.39 ((A12)PC4), P6.11, R38.1
/BILL_OUT_FULL: IC4.16 ((OC1B)PB6), P6.23, R50.1
/BILL_OUT_VALID: IC4.17 ((OC2/OC1C)PB7), P6.21, R49.1
/BILL_OUT_VEND1: IC4.42 ((A15)PC7), P6.5, R32.1
/BILL_OUT_VEND2: IC4.41 ((A14)PC6), P6.7, R33.1
/BILL_OUT_VEND3: IC4.40 ((A13)PC5), P6.9, R35.1
/CAN_SLEEP: IC1.8 (STB), IC2.2 (RE/), IC2.3 (DE), IC4.29 ((ICP1)PD4)
/COIN_INH: IC4.10 ((~SS~)PB0), P5.10, P5.13, P5.14, P5.15, P5.16, P5.17, R21.1, R31.2
/COIN_OUT_A: IC4.47 ((AD4)PA4), P5.1, R22.1
/COIN_OUT_B: IC4.46 ((AD5)PA5), P5.2, R23.1
/COIN_OUT_C: IC4.45 ((AD6)PA6), P5.9, R27.1
/COIN_OUT_D: IC4.44 ((AD7)PA7), P5.7, R26.1
/COIN_OUT_E: IC4.15 ((OC1A)PB5), P5.6, R25.1
/COIN_OUT_F: IC4.14 ((OC0)PB4), P5.4, R24.1
/COIN_OUT_MODE: P5.8, R20.1, R30.2
/DIGITAL_0: C19.1, IC4.51 ((AD0)PA0), R12.2, R58.1
/DIGITAL_1: C17.1, IC4.50 ((AD1)PA1), R14.2, R54.1
/DIGITAL_2: C15.1, IC4.49 ((AD2)PA2), R16.2, R48.1
/DIGITAL_3: C13.1, IC4.48 ((AD3)PA3), R18.2, R37.1
/JTAG TCK: IC4.57 (PF4(ADC4/TCK)), J4.11 (TCK/SCK)
/JTAG TDI: IC4.54 (PF7(ADC7/TDI)), J4.14 (TDI)
/JTAG TDO: IC4.55 (PF6(ADC6/TDO)), J4.16 (TDO)
/JTAG TMS: IC4.56 (PF5(ADC5/TMS)), J4.12 (TMS)
/LED A: IC4.33 (PG0(~WR~)), R64.1
/LED B: IC4.34 (PG1(~RD~)), R65.1
/LED C: IC4.43 (PG2(ALE)), R66.1
/LED RX: IC6.22 (CBUS1), R70.1
/LED TX: IC6.23 (CBUS0), R69.1
/MISO: IC4.13 ((MISO)PB3), J4.15 (TX/MISO)
/MOSI: IC4.12 ((MOSI)PB2), J4.13 (RX/MOSI)
/PDI: P7.4, R2.2
/PDO: P7.1, R4.2
/SCK: IC4.11 ((SCK)PB1), J4.6 (CAN+), P7.3
/SCL: IC4.25 ((SCL/INT0)PD0), R29.1, R39.2, R42.2, R44.2, R46.2
/SDA: IC4.26 ((SDA/INT1)PD1), R28.1, R36.1, R43.2, R45.2, R47.2
/UART0_CTS: IC4.5 (PE3(OC3A/AIN1)), IC5.10 (T2IN), IC6.11 (CTS)
/UART0_RTS: IC4.4 (PE2(XCK0/AIN0)), IC5.9 (R2OUT), IC6.3 (RTS)
/UART0_RX: IC5.12 (R1OUT), IC6.1 (TXD), R3.1
/UART0_TX: IC5.11 (T1IN), IC6.5 (RXD), R5.1
/UART1_CTS: IC3.10 (T2IN), IC4.31 ((T1)PD6)
/UART1_RTS: IC3.9 (R2OUT), IC4.30 ((XCK1)PD5)
/UART1_RX: IC1.4 (RXD), IC2.1 (RO), IC3.12 (R1OUT), IC4.27 ((RXD1/INT2)PD2)
/UART1_TX: IC1.1 (TXD), IC2.4 (DI), IC3.11 (T1IN), IC4.28 ((TXD1/INT3)PD3)
/USBID: R67.2
/USB_SLEEP: IC4.32 ((T2)PD7), R68.2
/strobe: IC4.8 (PE6(T3/INT6)), J4.10
/zero_cross: IC4.9 (PE7(IC3/INT7)), J4.8 (CAN-)
/~FLASH_EN~: IC4.18 (PG3(TOSC2)), JP1.1, R60.1
/~RST~: IC4.20 (~RESET), J4.9 (/RST), JP2.1, P7.5, R61.1
GND: C3.2, C4.2, C5.1, C6.1, C7.2, C8.2, C9.2, C10.1, C11.2, C12.2, C13.2, C14.2, C15.2, C16.2, C17.2, C18.2, C19.2, C20.2, C23.2, C24.2, C25.2, C26.2, C27.2, C28.2, C29.2, C30.2, C31.2, C32.2, C33.1, D1.1 (K), D2.1 (K), D3.1 (K), D4.1 (K), D5.1 (K), IC1.2 (GND), IC2.5 (GND), IC3.15 (GND), IC4.22 (GND), IC4.53 (GND), IC4.63 (AGND), IC5.15 (GND), IC6.7 (GND), IC6.18 (GND), IC6.21 (GND), IC6.25 (AGND), IC6.26 (TEST), J4.2 (GND), JP1.2, JP2.2, P1.3, P1.7, P1.11, P1.15, P2.1, P2.3, P2.5, P2.7, P3.1, P3.3, P3.5, P3.7, P4.1, P4.3, P4.5, P4.7, P5.3, P5.12, P6.2, P6.4, P6.6, P6.8, P6.10, P6.12, P6.14, P6.22, P6.24, P6.26, P7.6, P8.1, P9.1, P11.4 (GND), P12.5 (GND), P13.5, R8.1, R9.1, R11.1, R30.1, R31.1, R63.2, R71.1, TP1.1, TP2.1, TP3.1, TP4.1, U1.2 (GND)
unnamed: C1.1, IC3.1 (C1+)
unnamed: C1.2, IC3.3 (C1-)
unnamed: C2.1, IC3.4 (C2+)
unnamed: C2.2, IC3.5 (C2-)
unnamed: C4.1, IC4.62 (AREF), R1.1
unnamed: C5.2, IC4.23 (XTAL2), X1.1
unnamed: C6.2, IC4.24 (XTAL1), X1.2
unnamed: C8.1, IC3.2 (V+)
unnamed: C9.1, IC3.6 (V-)
unnamed: C21.1, IC5.1 (C1+)
unnamed: C21.2, IC5.3 (C1-)
unnamed: C22.1, IC5.4 (C2+)
unnamed: C22.2, IC5.5 (C2-)
unnamed: C25.1, IC6.17 (3V3OUT)
unnamed: C29.1, IC5.2 (V+)
unnamed: C30.1, IC5.6 (V-)
unnamed: D1.2 (A), R64.2
unnamed: D2.2 (A), R65.2
unnamed: D3.2 (A), R66.2
unnamed: D4.2 (A), R69.2
unnamed: D5.2 (A), R70.2
unnamed: IC1.5 (SPLIT), R6.2, R7.1
unnamed: IC1.6 (CANL), IC2.7 (B), IC3.13 (R1IN), P10.2, R6.1
unnamed: IC1.7 (CANH), IC2.6 (A), IC3.8 (R2IN), P10.7, R7.2
unnamed: IC3.7 (T2OUT), P10.8
unnamed: IC3.14 (T1OUT), P10.3, R8.2
unnamed: IC4.2 (PE0(RXD0/PDI)), R2.1, R3.2
unnamed: IC4.3 (PE1(TXD0/PDO)), R4.1, R5.2
unnamed: IC5.7 (T2OUT), P13.8
unnamed: IC5.8 (R2IN), P13.7
unnamed: IC5.13 (R1IN), P13.2
unnamed: IC5.14 (T1OUT), P13.3
unnamed: IC6.12 (CBUS4), R68.1
unnamed: IC6.15 (USBD+), P11.3 (D+), P12.3 (D+)
unnamed: IC6.16 (USBD-), P11.2 (D-), P12.2 (D-)
unnamed: IC6.19 (RESET), R62.2, R63.1
unnamed: J4.5 (SDA), R28.2
unnamed: J4.7 (SCL), R29.2
unnamed: P1.2, R12.1
unnamed: P1.4, R13.1
unnamed: P1.6, R14.1
unnamed: P1.8, R15.1
unnamed: P1.10, R16.1
unnamed: P1.12, R17.1
unnamed: P1.14, R18.1
unnamed: P1.16, R19.1
unnamed: P2.6, R42.1
unnamed: P2.8, R43.1
unnamed: P3.6, R44.1
unnamed: P3.8, R45.1
unnamed: P4.6, R46.1
unnamed: P4.8, R47.1
unnamed: P10.5, R9.2
unnamed: P10.6, R11.2
unnamed: P10.9, R10.2
unnamed: P11.1 (VCC), P12.1 (VCC), R62.1
unnamed: P11.5 (shield), P12.6 (shield), R71.2
unnamed: P12.4 (ID), R67.1
VAA: C11.1, IC4.64 (AVCC), L1.1, R1.2
VCC: C3.1, C7.1, C10.2, C20.1, C23.1, C24.1, C26.1, C27.1, C28.1, C33.2, IC1.3 (+5V), IC2.8 (VCC), IC3.16 (VCC), IC4.21 (VCC), IC4.52 (VCC), IC5.16 (VCC), IC6.4 (VCCIO), IC6.20 (VCC), J4.1 (5V), L1.2, P1.1, P1.5, P1.9, P1.13, P2.2, P2.4, P3.2, P3.4, P4.2, P4.4, P6.15, P6.17, P6.19, P7.2, P9.2, R20.2, R21.2, R22.2, R23.2, R24.2, R25.2, R26.2, R27.2, R32.2, R33.2, R34.2, R35.2, R36.2, R37.2, R38.2, R39.1, R40.2, R41.2, R48.2, R49.2, R50.2, R51.2, R52.2, R53.2, R54.2, R55.2, R56.2, R58.2, R60.2, R61.2, U1.3 (VO)


Board: 2 copper layers, 97.2 x 90.5 mm, 136 parts (0 on the bottom side), 118 nets.

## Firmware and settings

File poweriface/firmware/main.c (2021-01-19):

#include <inttypes.h>
#include <stdbool.h>
#include <avr/io.h>
#include <avr/interrupt.h>
#include <util/delay.h>
#include <can.h>
#include <messages.h>

static bool report_change = false;

static void init() {
	// Enable GPIO: PB2, PB3, PB4 output, low; PB5 input, pull-up on
 	PORTB = (PORTB & ~(_BV(PB2) | _BV(PB3) | _BV(PB4))) | _BV(PB5);
	DDRB = (DDRB & ~_BV(PB5)) | (_BV(PB2) | _BV(PB3) | _BV(PB4));
	
	// Initialize CAN interface
	can_init(BITRATE_125_KBPS);
	// Regular receive/transmit mode
	can_set_mode(NORMAL_MODE);

	// Filter for messages addressed to us (RTR on)
	can_filter_t us = {
		.id = CAN_HOSTID_POWER,
		.mask = CAN_HOSTID_MASK,
		.flags = {
			.rtr = 1,
			.extended = 0,
		},
	};
	can_set_filter(0, &us);
	// Filter for public messages (RTR off)
	can_filter_t pub = {
		.id = CAN_HOSTID_BROADCAST,
		.mask = CAN_HOSTID_MASK,
		.flags = {
			.rtr = 0,
			.extended = 0,
		},
	};
	can_set_filter(1, &pub);

	// Enable interrupts to start reception
	sei();
}


// UART bit-uart_bang 8 bits on the debug port, LSB first, 1 stop bit, no parity, 9600 baud
void uart_bang(uint8_t data) {
	// Start bit: low
	PORTB &= ~_BV(PB4);
	_delay_us(102);
	for (uint8_t i = 0; i < 8; i++) {
		// data bit
		if (data & (_BV(i))) {
			PORTB |= _BV(PB4);
		} else {
			PORTB &= ~_BV(PB4);
		}
		_delay_us(102);
	}
	// Stop bit: high (and stay there after)
	PORTB |= _BV(PB4);
	_delay_us(102);
}

// Bit-bang pattern (LSB first) out the data line
uint16_t bang(uint16_t data) {
	uint16_t in = 0;
	for (uint8_t i = 0; i < 16; i++) {
		// Data bit
		if (data & 1) {
			PORTB |= _BV(PB4);
		} else {
			PORTB &= ~_BV(PB4);
		}
		// Clock up
		PORTB |= _BV(PB2);
		_delay_us(4);
		// Clock down
		PORTB &= ~_BV(PB2);
		_delay_us(4);
		// Read
		if (PINB & _BV(PB5)) {
			in |= 1;
		}
		// Shift
		data >>= 1;
		in <<= 1;
	}
	// Clear data
	PORTB &= ~_BV(PB4);
	return in;
}

// Strobe output
void strobe() {
	// Strobe
	PORTB |= _BV(PB3);
	_delay_us(4);
	PORTB &= ~_BV(PB3);
}

static void send_status() {
	// Bit-bang register contents in (also send out zeros, but don't strobe)
	uint16_t status = bang(0);
	// Send the current state back out to prevent glitches
	bang(status);

	if (can_check_free_buffer()) {
		can_t msg = {
			.id = CAN_MSG_POWER_STATUS,
			.flags = {
				.rtr = 0,
			},
			.length = 2,
			.data = { (uint8_t) (status >> 8), (uint8_t) status, },
		};
		can_send_message(&msg);
	}
}

static void fire_relay(uint8_t num) {
	if (num == 0) {
		bang(0);
		strobe();
	} else if (num <= 5) {
		uint16_t out = 0x0080 >> (num - 1);
		bang(out);
		strobe();
	}
}

static void loop() {
	// Check for new messages
	if (can_check_message()) {
		can_t msg = { 0 };
		uint8_t status = can_get_message(&msg);
		if (status != 0) {
			switch (msg.id) {
			case CAN_MSG_POWER_STATUS:
				send_status();
				break;
			case CAN_MSG_POWER_DISPENSE:
				if (msg.length == 1) {
					// stop (d0 = 0) or fire relay (d0 = 1..5)
					fire_relay(msg.data[0]);
					// also send out the current status
					send_status();
				}
				break;
			case CAN_MSG_AUTO_STATUS:
				if (msg.length == 1) {
					report_change = msg.data[0] ? true : false;
				}
				break;
			}
		}
	}
}

int main() {
	init();
	while (1) {
		loop();
	}
}

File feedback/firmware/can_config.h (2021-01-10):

#ifndef	CONFIG_H
#define	CONFIG_H

#define CAN_CONFIG_LOADED

// -----------------------------------------------------------------------------
/* Global settings for building the can-lib and application program.
 *
 * The following two #defines must be set identically for the can-lib and
 * your application program. They control the underlying CAN struct. If the
 * settings disagree, the underlying CAN struct will be broken, with
 * unpredictable results.
 * If can.h detects that any of the #defines is not defined, it will set them
 * to the default values shown here, so it is in your own interest to have a
 * consistent setting. Ommiting the #defines in both can-lib and application
 * program will apply the defaults in a consistent way too.
 *
 * Select if you want to use 29 bit identifiers.
 */
#define	SUPPORT_EXTENDED_CANID	1

/* Select if you want to use timestamps.
 * Timestamps are sourced from a register internal to the AT90CAN.
 * Selecting them on any other controller will have no effect, they will
 * be 0 all the time.
 */
#define	SUPPORT_TIMESTAMPS		0


// -----------------------------------------------------------------------------
/* Global settings for building the can-lib.
 *
 * Select ONE CAN controller for which you are building the can-lib. 
 */
#define	SUPPORT_MCP2515			0
#define	SUPPORT_AT90CAN			1
#define	SUPPORT_SJA1000			0


// -----------------------------------------------------------------------------
/* Setting for MCP2515
 *
 * Declare which pins you are using for communication.
 * Remember NOT to use them in your application!
 * It is a good idea to use bits from the port that carries MOSI, MISO, SCK.
 */
#define	MCP2515_CS				B,4
#define	MCP2515_INT				B,2

// -----------------------------------------------------------------------------
// Setting for SJA1000

#define	SJA1000_INT				E,0
#define	SJA1000_MEMORY_MAPPED	1

// memory-mapped interface
#define	SJA1000_BASE_ADDR		0x8000		// for ATMega162

/*
// port-interface
#define	SJA1000_WR				D,6
#define	SJA1000_RD				D,7

#define	SJA1000_ALE				E,1
#define	SJA1000_CS				C,0
#define	SJA1000_DATA			A
*/

// -----------------------------------------------------------------------------
// Setting for AT90CAN

// Number of CAN messages which are buffered in RAM additinally to the MObs
#define CAN_RX_BUFFER_SIZE		16
#define CAN_TX_BUFFER_SIZE		8

// only available if CAN_TX_BUFFER_SIZE > 0
#define CAN_FORCE_TX_ORDER		1

#endif	// CONFIG_H

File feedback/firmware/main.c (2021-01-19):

#include <inttypes.h>
#include <avr/io.h>
#include <avr/interrupt.h>
#include <util/delay.h>
#include <can.h>
#include <messages.h>

static bool report_change = false;
static uint16_t saved_status;

static void init() {
	// Set PB as input, pull-up off
	DDRB = 0;
	// Set PC0/4/6 as input, pull-up off
	DDRC &= ~(_BV(DDC0) | _BV(DDC4) | _BV(DDC6));
	
	// Initialize CAN interface
	can_init(BITRATE_125_KBPS);
	// Regular receive/transmit mode
	can_set_mode(NORMAL_MODE);

	// Filter for messages addressed to us (RTR on)
	can_filter_t us = {
		.id = CAN_HOSTID_FEEDBACK,
		.mask = CAN_HOSTID_MASK,
		.flags = {
			.rtr = 1,
			.extended = 0,
		},
	};
	can_set_filter(0, &us);
	// Filter for public messages (RTR off)
	can_filter_t pub = {
		.id = CAN_HOSTID_BROADCAST,
		.mask = CAN_HOSTID_MASK,
		.flags = {
			.rtr = 0,
			.extended = 0,
		},
	};
	can_set_filter(1, &pub);

	// Enable interrupts to start reception
	sei();
}

static uint16_t get_status() {
	// Get GPIO state
	// PB -> invert -> Dend..Hend, Dempty..Fempty
	uint8_t statusl = ~PINB;
	// PC0,6,4 -> invert -> Gempty, Hempty, Reset
	uint8_t pinc = ~PINC;
	uint8_t gempty = (pinc & _BV(0)) ? _BV(0) : 0;
	uint8_t hempty = (pinc & _BV(6)) ? _BV(1) : 0;
	uint8_t swres = (pinc & _BV(4)) ? _BV(2) : 0;
	uint8_t statush = gempty | hempty | swres;

	return ((uint16_t) statush << 8) | ((uint16_t) statusl);
}

static void send_status(uint16_t status) {
	if (can_check_free_buffer()) {
		can_t msg = {
			.id = CAN_MSG_FEEDBACK_STATUS,
			.flags = {
				.rtr = 0,
			},
			.length = 2,
			.data = { (uint8_t) (status >> 8), status & 0xff, },
		};
		can_send_message(&msg);
	}
}

static void loop() {
	// Check for status changes
	uint16_t new_status = get_status();
	if (new_status != saved_status) {
		if (report_change) {
			send_status(new_status);
		}
		saved_status = new_status;
	}

	// Check for new messages
	if (can_check_message()) {
		can_t msg = { 0 };
		uint8_t status = can_get_message(&msg);
		if (status != 0) {
			switch (msg.id) {
			case CAN_MSG_FEEDBACK_STATUS:
				send_status(get_status());
				break;
			case CAN_MSG_AUTO_STATUS:
				if (msg.length == 1) {
					report_change = msg.data[0] ? true : false;
				}
				break;
			}
		}
	}
}

int main() {
	init();
	while (1) {
		loop();
	}
}

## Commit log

2015-04-01 First prototype all-in-one schema
    [power.sch]
2015-04-01 Updated schema with more complete circuit
    [power.sch]
2015-04-01 Added zero crossing detector circuit simulation graph
2015-04-01 Added KiCad library cache with missing parts
2015-04-02 Added redesigned control board schema and PCB layout
    [control.brd, control.sch]
2015-04-02 Added board layout for smaller DB9 sockets
    [control_smalldb9.kicad_pcb]
2015-04-02 Unified silk screen text sizes, fixed and relocated some text
    [control_smalldb9.kicad_pcb]
2015-04-02 Fixed a number of errata in first control board revision Swapped USB B port D+ and D- lines Swapped UART0 RX and TX lines Changed resistor values Added UART0 RX and TX LEDs Conntected USB sleep contr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
    [control.sch]
2015-04-02 Added global KiCad project
2015-04-03 Updated large DB9 socket PCB with errata from schema
    [control.brd]
2015-04-03 Added component library Updated conmponents in schematic Changed resistors and capacitors to standard symbol
    [control.sch]
2015-04-03 Fixed banknote scanner connector erratum, short circuit on power lines
    [control.sch]
2015-04-03 Updated schematic revision and copyright
    [control.sch]
2015-04-05 Added module library Fixed up schema with new part names Partial PCB redesign, incorporated schematic changes and errata Made PCB slightly smaller
    [control.brd, control.sch]
2015-04-06 Updated PCB Placed part labels Moved some parts to use space more efficiently
    [control.brd, control.sch]
2015-04-06 Converted board to new KiCAD format
    [control.kicad_pcb]
2015-04-06 Removed previous PCB layout
    [control_smalldb9.kicad_pcb]
2015-04-06 Added copyright field and OSHW logo to PCB
    [control.kicad_pcb]
2015-04-07 Removed PCB in old KiCAD format
    [control.brd]
2015-09-08 Moved circuit diagrams into separate directories Updated module library paths
    [control.kicad_pcb, control.sch, power.sch]
2015-09-08 Added power board circuit diagrams and PCB design (sto)
    [logic_psu.sch, matemat_power.brd, matemat_power.sch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]
2015-09-08 Added project file for old power board design
2015-09-08 Removed old power board circuit
    [power.sch]
2015-09-08 Added file cloning scripts for power board (sto)
2015-11-05 Updated control board for KiCad 4.0
    [control.kicad_pcb, control.sch]
2015-12-29 Removed pulldown resistors from analog/digital I/O block to save some space. Removed leftover reference from conversion to KiCad 4.
    [control.kicad_pcb, control.sch]
2015-12-30 Added new connection blocks for coin and banknote scanners
    [control.sch]
2015-12-30 Moved DB9 connectors in the schematic a little to clean up the trace mess
    [control.sch]
2015-12-30 Removed old coin and banknote connection block in schematic, rewired MCU for new block
    [control.sch]
2015-12-30 Added optional linear regulator for 5V Vcc. Replaced old connector symbols with current ones from the KiCad library.
    [control.sch]
2015-12-30 Updated layout with new/changed parts
    [control.kicad_pcb, control.sch]
2015-12-31 Added SOT-223 package to module library (currently missing from Debian)
2019-04-01 WIP control board rewiring to make it smaller
    [control.kicad_pcb, control.sch]
2019-04-01 Power board lib autocleanup
2019-04-01 Update and cleanup for KiCAD 5
    [control.kicad_pcb, control.sch]
2019-04-01 Updated power board for KiCAD 5
    [logic_psu.sch, matemat_power.sch, outputs.sch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]
2019-04-01 Made board smaller and started rerouting
    [control.kicad_pcb]
2019-04-01 Added recovered footprints back
2019-04-01 More rerouting
    [control.kicad_pcb]
2019-04-03 Added CAN extension for power board
    [poweriface.kicad_pcb, poweriface.sch]
2019-04-04 Connected hispeed control to GPIO pin
    [poweriface.kicad_pcb, poweriface.sch]
2019-04-04 Fixed small power plane issues
    [poweriface.kicad_pcb, poweriface.sch]
2019-04-09 Updated annotations
    [poweriface.kicad_pcb, poweriface.sch]
2019-04-09 Replaced crystal footprint with less wasteful one
    [poweriface.kicad_pcb, poweriface.sch]
2019-04-13 Added CAN sensor board
    [sensor.kicad_pcb, sensor.sch]
2019-04-13 Added power LED to sensor board
    [sensor.kicad_pcb, sensor.sch]
2020-07-19 Added ground terminals
    [poweriface.kicad_pcb, poweriface.sch]
2020-07-19 Recreated rescue library
    [logic_psu.sch, matemat_power.sch, outputs.sch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]
2020-07-26 poweriface: improve labeling
    [poweriface.kicad_pcb]
2020-07-26 sensor: modernize
    [sensor.kicad_pcb, sensor.sch]
2020-07-26 ignore board plots
2020-08-06 Added old wiring diagram
    [wiring.sch]
2020-08-24 wiring: Added some descriptions
    [wiring.sch]
2020-08-24 feedback: Added switch interface board
    [feedback.kicad_pcb, feedback.sch]
2020-08-24 drive: Added single-motor control board
    [drive.kicad_pcb, drive.sch]
2020-09-05 feedback: added separate terminal header
    [feedback.kicad_pcb, feedback.sch]
2020-12-01 fb: removed min clearance
    [feedback.kicad_pcb]
2020-12-01 drive: optimized routing and power plance placement
    [drive.kicad_pcb, drive.sch]
2020-12-08 Replace power pins with mini-fit jr
    [drive.kicad_pcb, drive.sch]
2021-01-05 Replaced BAS-40 with BAS-70 to avoid peak-peak overvoltage
    [drive.kicad_pcb, drive.sch]
2021-01-10 Updated LM317L part from library
    [drive.kicad_pcb, drive.sch]
2021-01-10 Added power interface test program
2021-01-10 Added build instructions for poweriface firmware
2021-01-13 Overhauled readme and added protocol and wiring information
2021-01-13 Sensor status report needs a dedicated ID
2021-01-17 Added feedback board firmware
2021-01-17 Adapted poweriface firmware to use new specs
2021-01-17 Cleaned up schematics and removed obsolete parts
    [logic_psu.sch, matemat_power.sch, outputs.sch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]
2021-01-18 Send out status after firing a relay
2021-01-19 Updated PCB layout
    [logic_psu.sch, matemat_power.brd, matemat_power.kicad_pcb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]
2021-01-24 Replaced power board diode pad layouts
    [logic_psu.sch, matemat_power.kicad_pcb, outputs.sch]

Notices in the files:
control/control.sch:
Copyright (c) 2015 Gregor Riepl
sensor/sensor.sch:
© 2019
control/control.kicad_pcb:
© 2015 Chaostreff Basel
